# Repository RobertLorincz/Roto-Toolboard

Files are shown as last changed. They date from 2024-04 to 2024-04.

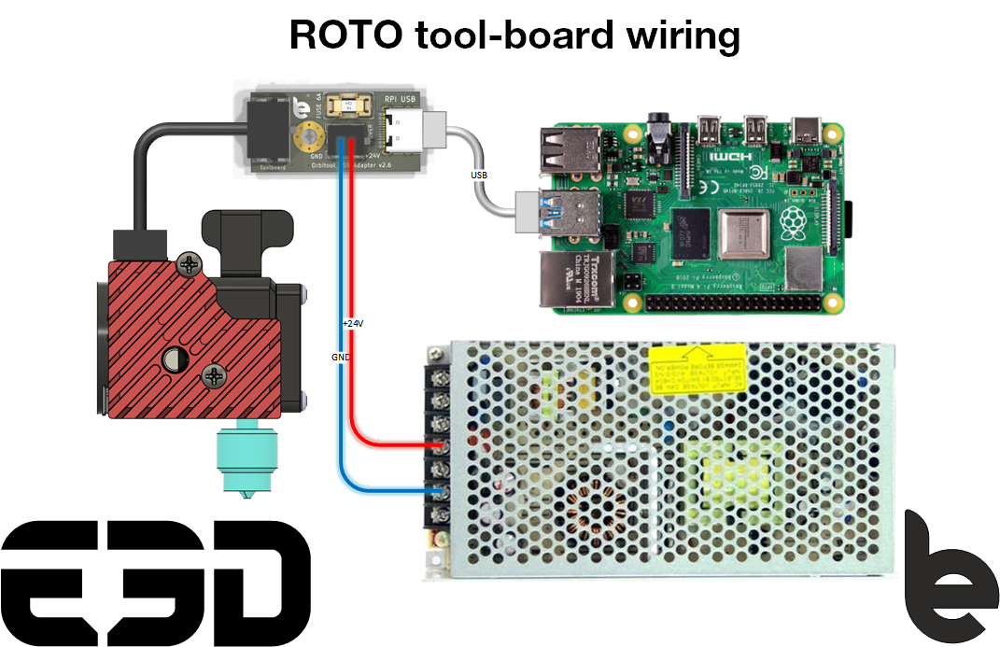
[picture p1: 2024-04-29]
Documentation/RotoTool-board Wiring.png

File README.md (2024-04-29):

# Roto-ToolboardRotoTool v1 4 v7
RotoTool v1 4 v73
RotoTool v1 4 v71

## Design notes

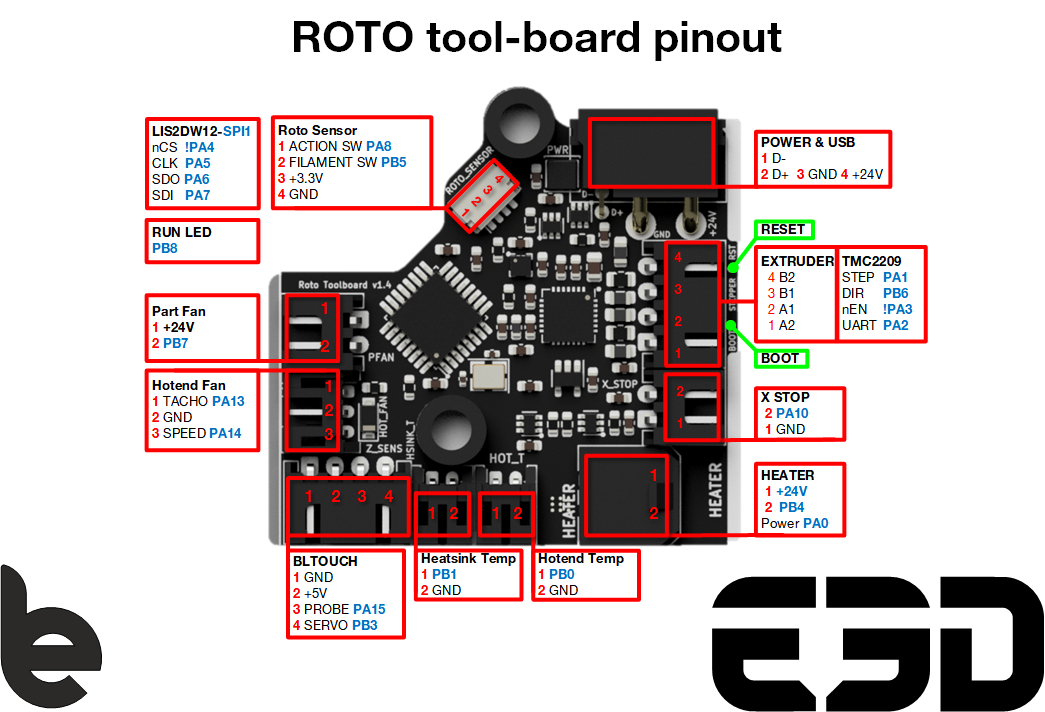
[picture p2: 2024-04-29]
Documentation/RotoTool-board Pinout.png

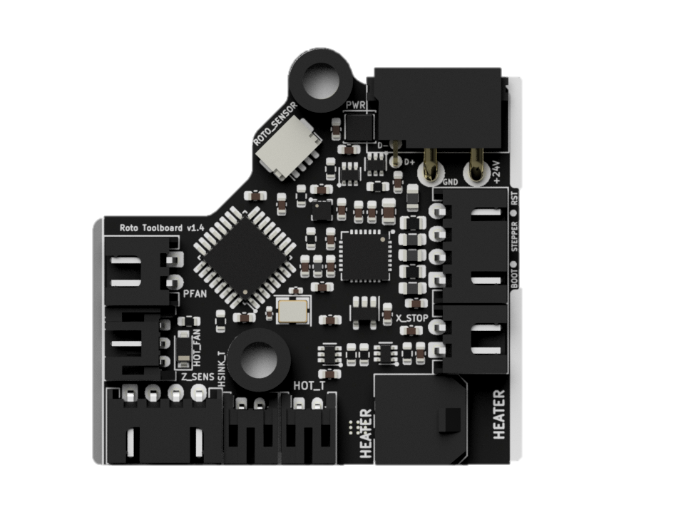
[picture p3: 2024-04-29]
Pictures/roto back.png

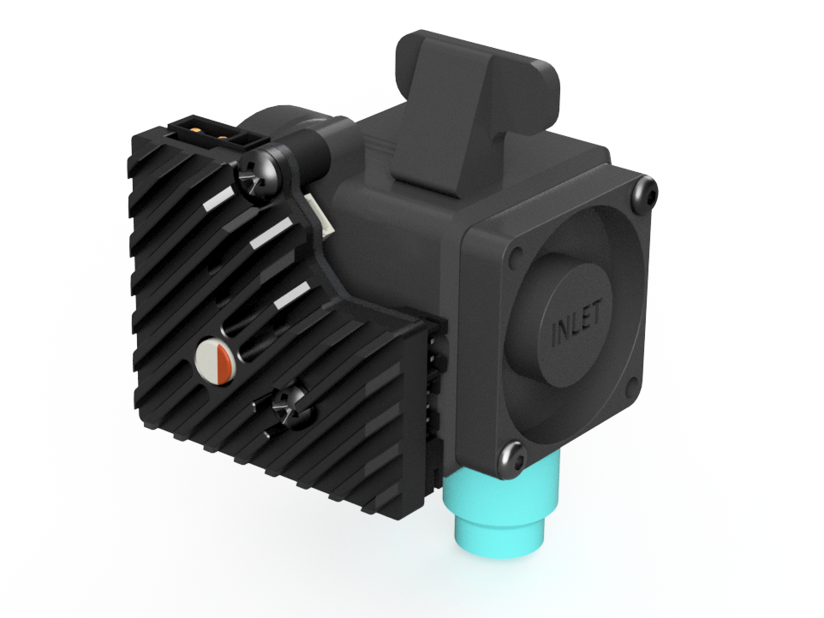
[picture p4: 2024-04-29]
Pictures/RotoTool v1.4 p1.png

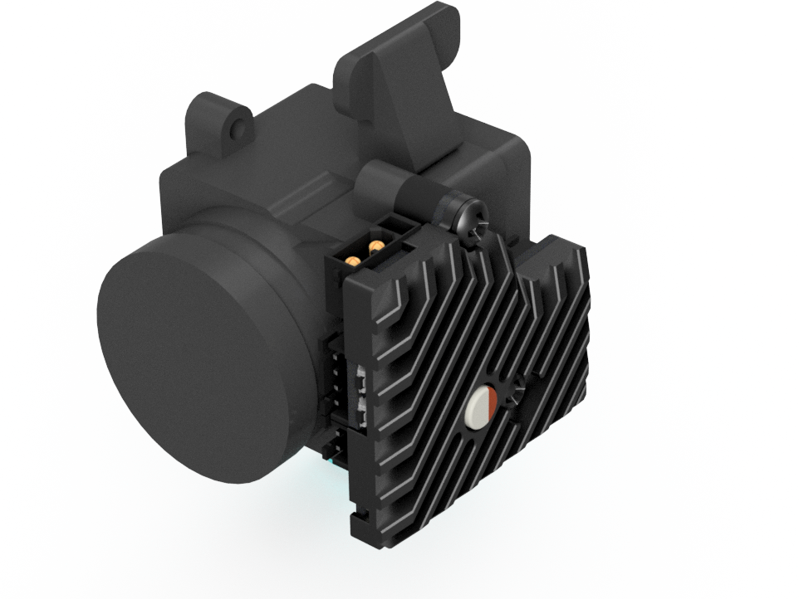
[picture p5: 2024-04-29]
Pictures/RotoTool v1.4 p2.png

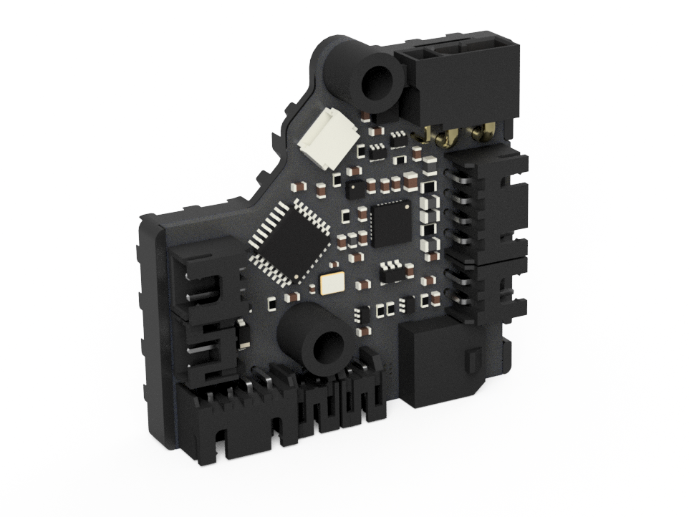
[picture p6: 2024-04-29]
Pictures/RotoTool v1.4 p3.png

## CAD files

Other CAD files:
3D CAD/RotoTool v1.4.f3d

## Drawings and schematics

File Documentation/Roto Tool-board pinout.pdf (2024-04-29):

### Power Supply

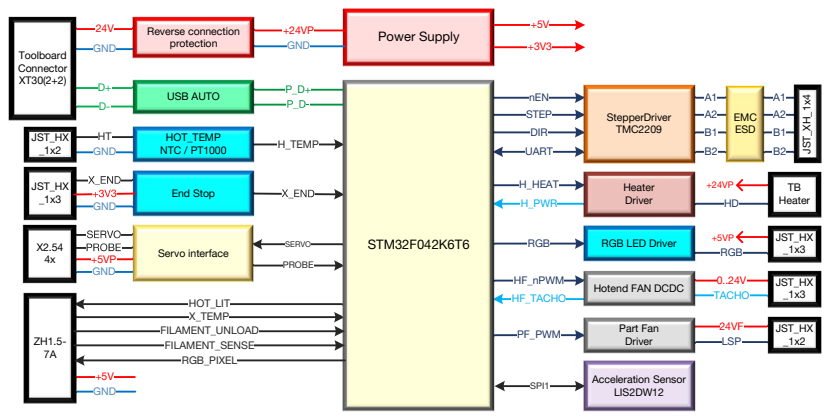
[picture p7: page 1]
nEN STEP DIR; UART; JST_XH_1x4 EMC; ESD; H_HEAT; H_PWR; Heater; Heater Driver; StepperDriver TMC2209; RGB; +5VP RGB; HF_nPWM HF_TACHO; 0..24V TACHO; PF_PWM; 24VF LSP; JST_HX _1x3; JST_HX _1x2; Part Fan Driver; GND; +24VP GND; HT GND; H_TEMP; HOT_LIT X_TEMP; SERVO; PROBE GND; SPI1; Toolboard Connector XT30(2+2); STM32F042K6T6 Servo interface; End Stop; HOT_TEMP NTC / PT1000; USB AUTO; Acceleration Sensor LIS2DW12; Reverse connection protection; FILAMENT_UNLOAD FILAMENT_SENSE RGB_PIXEL

RGB LED Driver

Hotend FAN DCDC

### POWER & USB

### LIS2DW12-SPI1

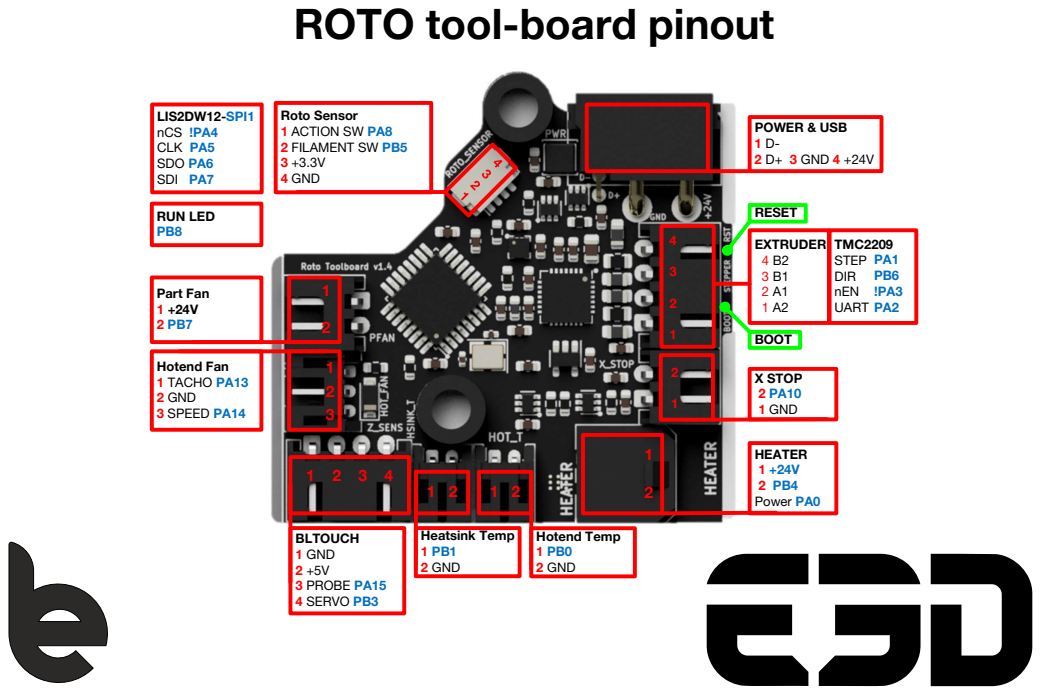
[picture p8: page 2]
X STOP 2 PA10 1 GND; EXTRUDER 4 B2 3 B1 2 A1 1 A2; BLTOUCH 1 GND 2 +5V 3 PROBE PA15 4 SERVO PB3; BOOT; RESET; Hotend Fan 1 TACHO PA13 2 GND 3 SPEED PA14; Hotend Temp 1 PB0 2 GND; 1 D- 2 D+ 3 GND 4 +24V; TMC2209 STEP DIR nEN UART; HEATER 1 +24V 2 PB4 Power PA0; Heatsink Temp 1 PB1 2 GND; nCS !PA4 CLK PA5 SDO PA6 SDI PA7; Part Fan 1 +24V 2 PB7; Roto Sensor 1 ACTION SW PA8 2 FILAMENT SW PB5 3 +3.3V 4 GND; RUN LED PB8

ROTO tool-board pinout

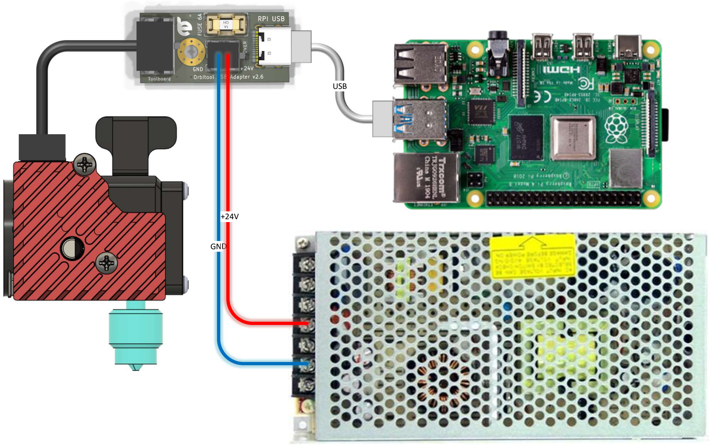
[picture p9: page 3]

GND

+24V

USB

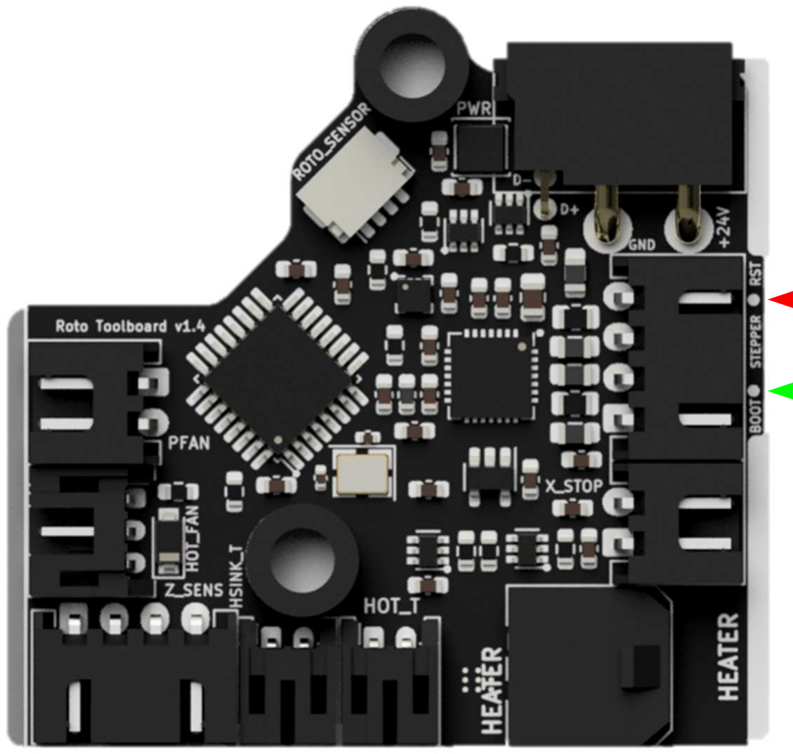
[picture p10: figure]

### BOOT

### RESET

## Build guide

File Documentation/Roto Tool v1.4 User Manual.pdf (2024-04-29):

# Rototool v1.4

Should a tool-board magic smoke come out because of user error? Why?

Should a tool-board be destroyed by a fault in your 3D printer? Why?

My answer is NO! And this is what this tool-board is all about!

We are hobbits, professionals and let’s face it, we do mistakes, and when the magic smoke shows up everybody is disappointed, even if we know it’s a user fault. In this board, I promise you the magic smoke is kept inside extremely tight!

Smokeless Features

- Optimized for E3D Roto extruder shape and features
- STM32F042 microcontroller running on 48MHz
- Automotive USB communication with Raspberry PI
- Onboard LIS2DW12 accelerometer
- TMC2209 extruder stepper driver
- Direct connection to Roto
- 1 x PWM 24V controlled part fan output
- 1 x PWM 5V controlled extruder fan output with RPM speed input signal
- Hot-end temperature sensor input compatible with standard NTC or PT1000 temperature sensor types
- I/O for bed level sensing
- X-Stop sensor input
- Tool-board and extruder temperature sensor
- | Advanced | thermal | management
| system

Protection Features

- Active short circuit protected Hot-end output
- Active short circuit protected fan driver outputs
- Active Protection circuit against reverse power supply connection
- Protection against loss of GND supply
- Analog and digital inputs protected against short to +24V supply voltage
- USB data lines protected against short circuits to GND and +24V
- EMI interference and ESD protection an all inputs and outputs
- Heater thermal runaway protection in case of short between heater and sense thermistor wires

Author: Dr. Róbert Lőrincz

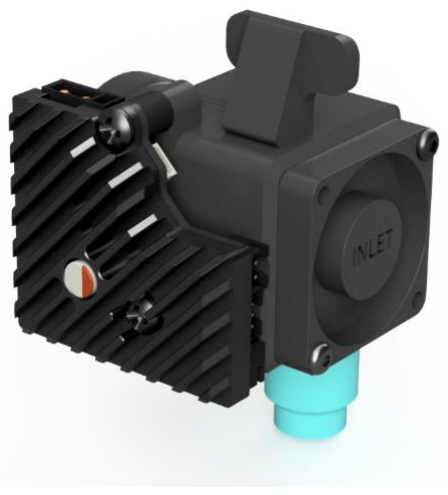
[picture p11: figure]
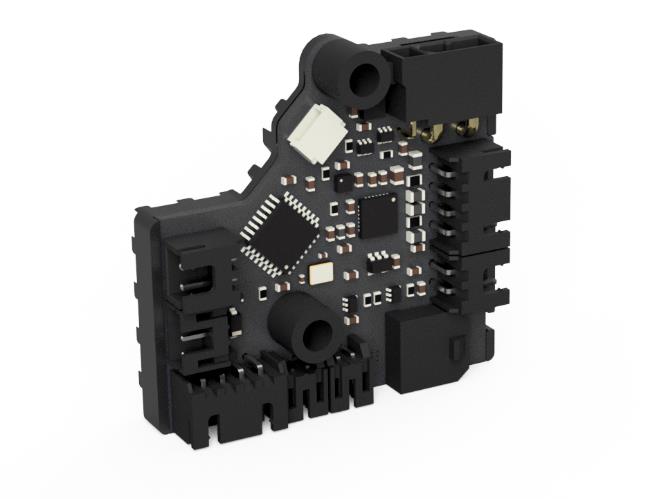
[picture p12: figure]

ROTOTOOL V1.4 | 04/29/2024

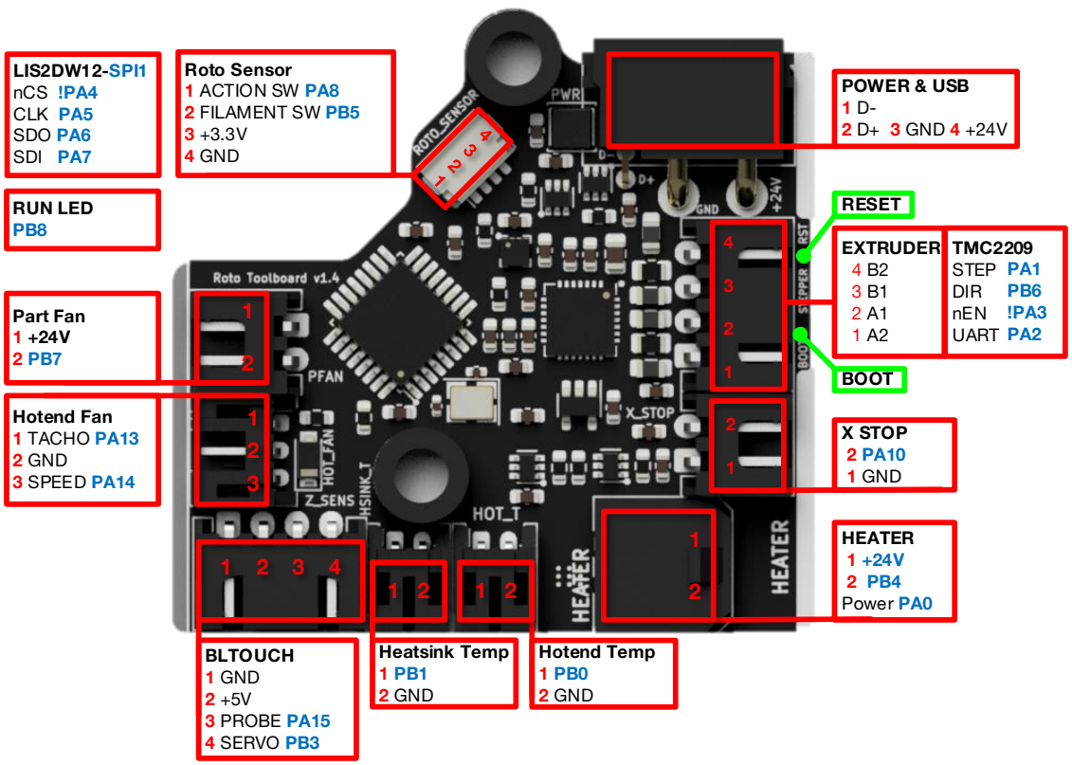
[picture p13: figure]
X STOP 2 PA10 1 GND; EXTRUDER 4 B2 3 B1 2 A1 1 A2; BLTOUCH 1 GND 2 +5V 3 PROBE PA15 4 SERVO PB3; BOOT; RESET; Hotend Fan 1 TACHO PA13 2 GND 3 SPEED PA14; Hotend Temp 1 PB0 2 GND; POWER & USB 1 D- 2 D+ 3 GND 4 +24V; TMC2209 STEP DIR nEN UART; HEATER 1 +24V 2 PB4 Power PA0; Heatsink Temp 1 PB1 2 GND; LIS2DW12-SPI1 nCS !PA4 CLK PA5 SDO PA6 SDI PA7; Part Fan 1 +24V 2 PB7; Roto Sensor 1 ACTION SW PA8 2 FILAMENT SW PB5 3 +3.3V 4 GND; RUN LED PB8

LORINCZ ELECTRONICS | DOCUMENT VERSION V1.0 | 2
www.orbiterprojects.com

# 1 Pinout definition

# 2 Features description

# 2.1Introduction

For me electrical robustness of a design is part of the requirements. One of my main design goals was to integrate protection against common user errors and 3D printer defects.

In the end nothing is more frustrating than powering up your new board and let the magic smoke out. Even if is due to user fault the disappointment will still be present.

This design is based on automotive technology where protection to all kind of hazards is state of the art long time ago.

This document describes the main specific features of the tool-board.

# 2.2 Power supply concept

The board is supplied via XT30(2+2) connector which includes the +24V, GND, USB_DATA+ and USB_DATA- signals.

From the connector the board is supplied via a reverse power supply protection circuit. This prevents the tool-board damage in case of accidental reversed supply by user error, the board will not start up it will behave like it’s not powered.

The microcontroller is supplied from a 3.3V LDO supplied from the onboard 5V DC-DC buck converter for the highest power supply efficiency and lowest possible power consumption.

# 2.3USB communication interface

The tool-board is equipped with automotive grade USB interface. The main difference being the higher electrical robustness of the automotive USB, still keeping high communication speed possible. Therefore, in case of short to GND or up to +28V of the USB data lines will not cause any destruction and will work properly after the short circuit is removed.

The same circuit offers protection in case of GND connection loss, which will lead to biasing all the communication signals to the supply positive line (in our case +24V).

The USB interface of the Raspberry PI is not robust against these electrical hazards which may occur in a 3D printer. Therefore, the tool-board shall be supplied and connected to the Raspberry Pi using the supplied adapter board, which has the onboard protection circuits to protect the Raspberry PI USB port.

Next picture presents the tool-board wiring connection principle.

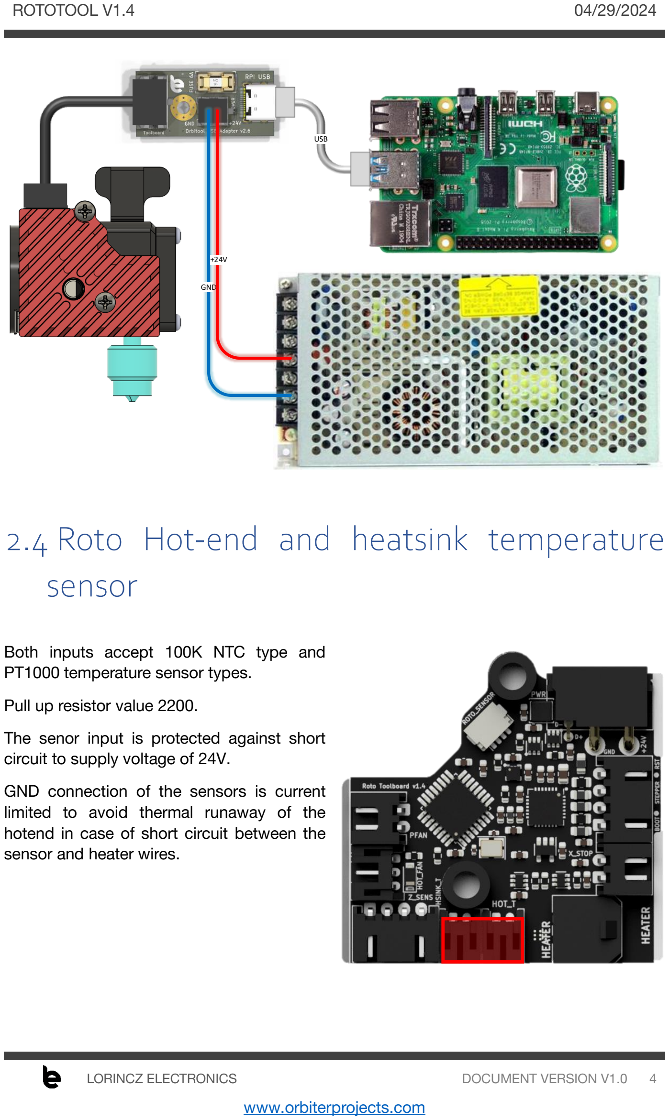
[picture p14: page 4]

GND

+24V

USB

# 2.4 Roto Hot-end and heatsink temperature sensor

Both inputs accept 100K NTC type and PT1000 temperature sensor types.

Pull up resistor value 2200.

The senor input is protected against short circuit to supply voltage of 24V.

GND connection of the sensors is current limited to avoid thermal runaway of the hotend in case of short circuit between the sensor and heater wires.

# 2.5 Driver circuit for hot-end heater

The hot-end heater driver circuit is
implemented with active protection against short circuits.

The circuit measures the heater current and in case the current rises over a predefined threshold iOC_HOT it switches OFF the heater MOSFET until the next PWM cycle to prevent damage.

The heater max power shall be limited to 99.5% meaning max_power: 0.995 to avoid driver stuck in protection mode due to an unlikely event a fake error detection.

The heater current is feedback to Klipper

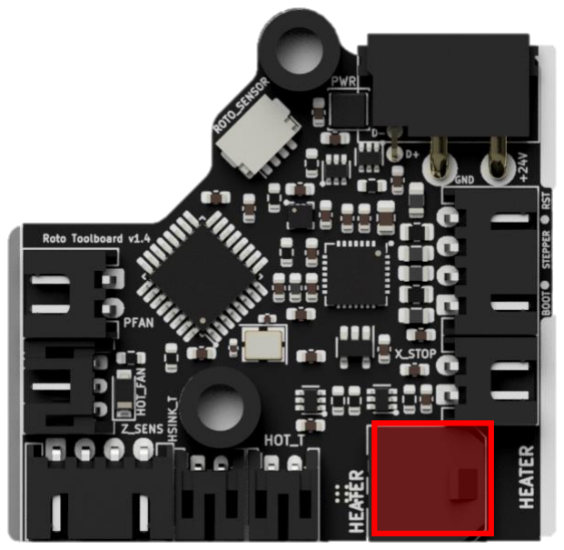
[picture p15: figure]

which can calculate the actual power consumption of the heater element. This can be used to detect failures of the heater element like short circuit or loss of heating power.

You may say yes, other boards have also protection with onboard fuses. Well, that is simply not enough to protect MOSFETs from being damaged because fuses have long reaction time, about 1-2s range. Their mission is to protect the circuit from catching fire in case of a defect but it cannot protect the heater driver MOSFET from getting destroyed. This active protection reacts within 10ms ensuring the driver stage is switched off before it gets damaged due to a short circuit or overload event.

To display the actual power of the heater, include the following section:

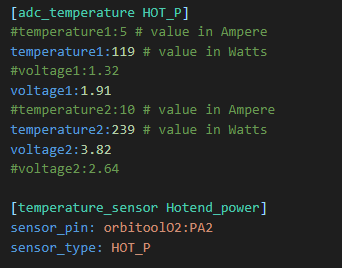
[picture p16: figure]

The hot-end power or current can be displayed based on preference. The power is calculated considering 24V power supply.

# 2.6 Part fan driver output

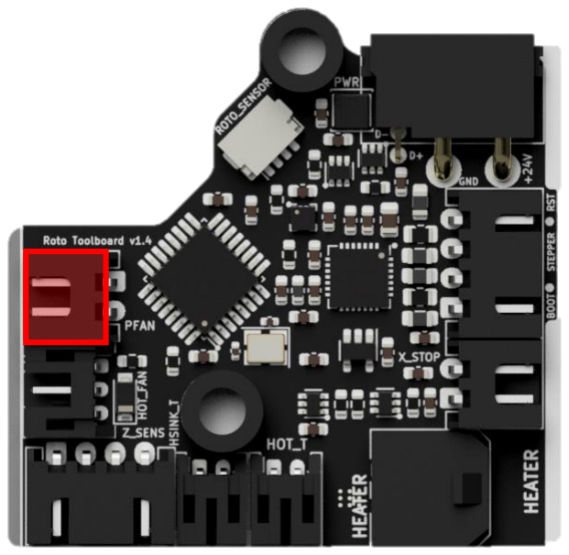
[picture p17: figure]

The part fan driver has a similar protection circuit like the hot-end driver, in case of overcurrent the fan driver is switched OFF until the next PWM cycle.

The PWM duty cycle of the fan driver shall be limited to 99.5% meaning max_power: 0.995 to avoid fan driver stuck in OFF state due to an unlikely event a fake error detection.

Configuration of the Fan driver:

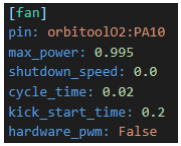
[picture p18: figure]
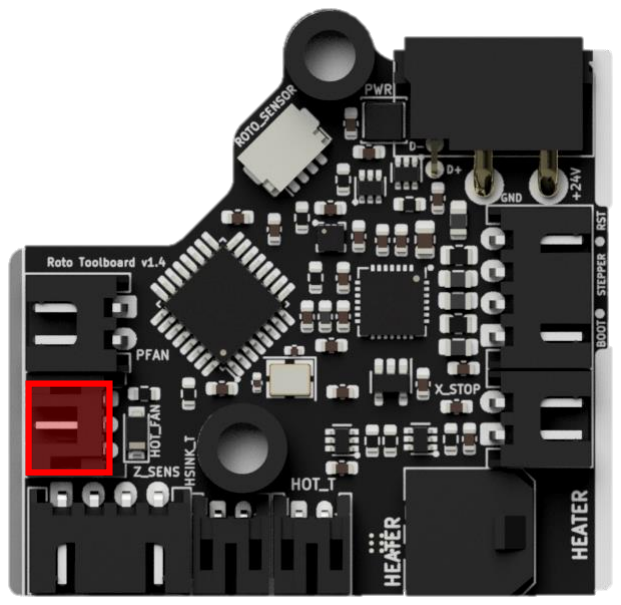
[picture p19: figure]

# 2.7Hot-end fan output

The Roto is equipped with a 5V supplied cooling fan.

The fan output current is limited to 500mA.

The fan speed input signal is feed back to the microcontroller for FAN RPM measurement, however for a reliable speed signal the Roto cooling fan shall be used in ON / OFF mode, without PWM control.

# 3 Microcontroller programming

1. Connect the board to the host Raspberry Pi via USB adapter cable.

### 2. This step depends on if your board has firmware on it or not already:

a) If you have a pre-flashed board first must enter DFU mode as follows:
- press the BOOT and RESET switch,
- release the RESET while keeping the BOOT button pressed,
- release BOOT switch button after 3 seconds.
b) If you have a new un-flashed board:
- The MCU default's to DFU mode if there is no other firmware installed, confirm the board enters DFU mode in step 4

BOOT

RESET

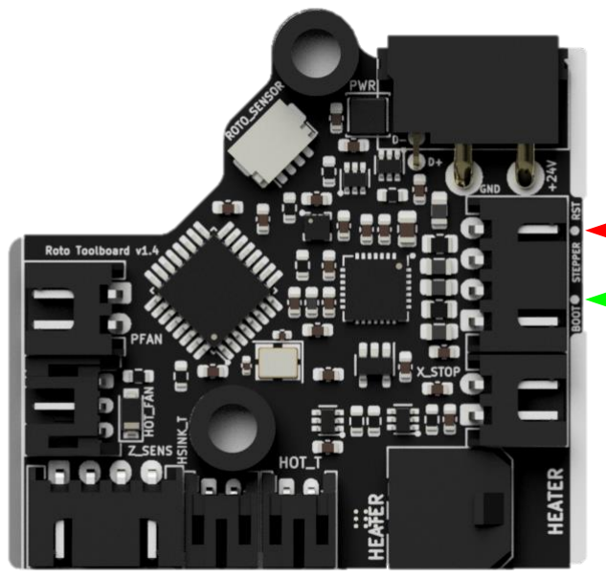
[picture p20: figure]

### 3. Connect to your host raspberry pi via SSH 4. Run lsusb from the command prompt

- Make sure you see an STM32 in DFU mode listed

### 5. Run dfu-util --list from the command prompt

- note the text inside the [xxxx:yyyy]

### 6. Run cd ~/klipper from the command line to enter the Klipper directory 7. Run make menuconfig settings should be:

- Cristal oscillator – 8Mhz

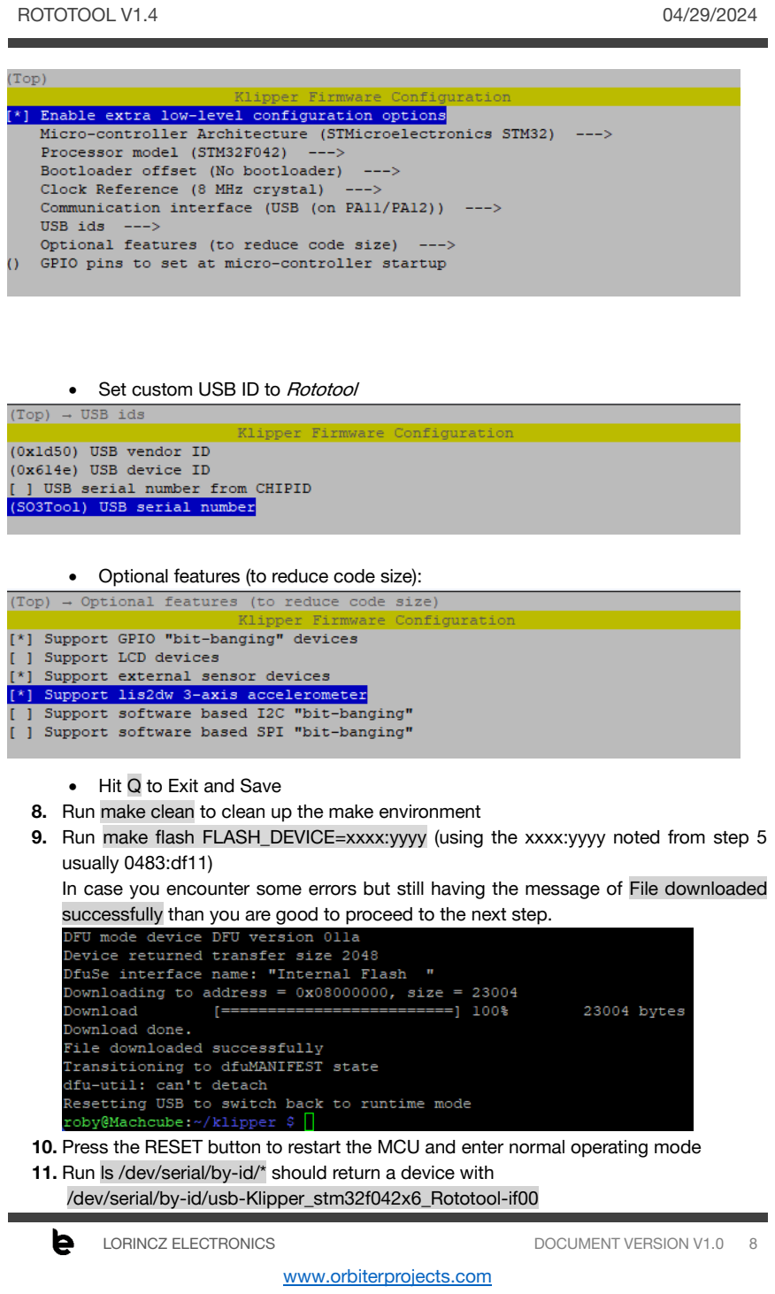
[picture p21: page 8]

- Set custom USB ID to Rototool
- Optional features (to reduce code size):
- Hit Q to Exit and Save

### 8. Run make clean to clean up the make environment

9. Run | make flash FLASH_DEVICE=xxxx:yyyy | (using the xxxx:yyyy noted from step 5
usually 0483:df11)
In case you encounter some errors but still having the message of File downloaded successfully than you are good to proceed to the next step.

### 10. Press the RESET button to restart the MCU and enter normal operating mode 11. Run ls /dev/serial/by-id/* should return a device with

/dev/serial/by-id/usb-Klipper_stm32f042x6_Rototool-if00

Copy this virtual serial port name to the Rototool config file MCU section

Your tool-board should now be usable with Klipper. Use the example config file to get started. Best option is to copy the config file into the same directory as printer.cfg.
Add [include Rototool.cfg] to the beginning of your printer.cfg to include the file.
Comment out the unused I/O features of the Rototool config section.

# 4 Electrical characteristics

# 4.1Absolute maximum ratings

Important Note: The Rototool board can withstand these limits without electrical damage, however long-term exposition to these limits is not recommended. Device absolute maximum rating is not the same with functional range.

The maximum ratings may not be exceeded under any circumstances!

Table 1 Rototool absolute maximum ratings

Nr. | Parameter | Min | Max | Unit
A1 | Temperature range | -20 | 85 | °C
A2 | Supply voltage | -30 | 30 | V
A3 | Extruder stepper current | | 1 | A
A4 | Hot-end heater current | | 6.8 | A
A5 | Part fan output current | | 1 | A
A6 | Hot-end Fan | | 0.5 | A
A7 | USB Data lines | -1 | 28* | V
A8 | Hot-end and extruder temperature sensor input | -1 | 28* | V
A9 | End stop sensor input | -1 | 28* | V
A10 | Z sensor I/O interface | -10 | +15 | V
A11 | Roto sensor interface inputs | -1 | 24 | V
A12 | ESD-Protection level for handling (Human Body Model, HMB) | -8 | 8 | kV
*Should not exceed the supply voltage

# 4.2 Full functional operational limits

Table 2 Rototool electrical characteristics

Nr. | Parameter | Symbol | Min | Typ | Max | Unit
| General
P1 | Operating temperature range | to | -20 | 60 | °C
P2 | Max ambient temperature with active cooling | to_cooled | | 80 | °C
P3 | Power supply voltage | vPWR | 22 | 28 | V
P4 | Power supply voltage measurement accuracy | aPWR | -3 | 3 | %
| Extruder stepper
P5 | Extruder stepper current (max 60°C chamber temp) | iMOT_60 | | 0.85* | A
P6 | Extruder stepper current (max 80°C chamber temp) | iMOT_80 | 0.5 | 0.6 | A
| Hot-end heater
P7 | Hot-end heater nominal current | iHEATER | | | 5 | A
P8 | Hot-end heater overcurrent switch OFF threshold | iOV_HOT | 5.9 | 6.8 | 7.2 | A
P9 | Hot-end overcurrent detection time | tOV_HOT | | | 10 | ms
P10 | Hot-end power measurement accuracy | aP_HOT | -6 | | 6 | %
| Part Fan
P11 | Part fan output current | iPART_FAN | | | 1 | A
P12 | Part fan overcurrent switch OFF threshold | iOC_PART | 1.2 | 2 | 2.5 | A
P13 | Part fan overcurrent detection time | tOC_PART | | | 5 | ms
P14 | Part fan PWM frequency | fPART_FAN | | 100 | | Hz
| Hot-end Cooling fan
P15 | Hot-end fan output current | iHOT_FAN | | 0.5 | A
P16 | Hot-end fan current limitation | iCL_HOT_FAN | 0.5 | | A
| Internal supplies
P19 | Internal 5V supply protection current limitation | iSC_5V | 2 | 3 | 3.9 | A
P20 | Internal 3.3V supply protection current limitation | iSC_3V3 | 220 | 350 | 550 | mA
*Parameter derating with ambient temperature
